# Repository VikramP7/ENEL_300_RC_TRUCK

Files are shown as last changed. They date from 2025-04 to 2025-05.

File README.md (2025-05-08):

*<div align="right"> Vikram Procter, Caleb Garcia, Graham Coleman, Devon Calvin | Feb 12, 2025 </div>*

# DIDSBURY DIDDLERS & Co. Est. 2006 - README

## Project Overview
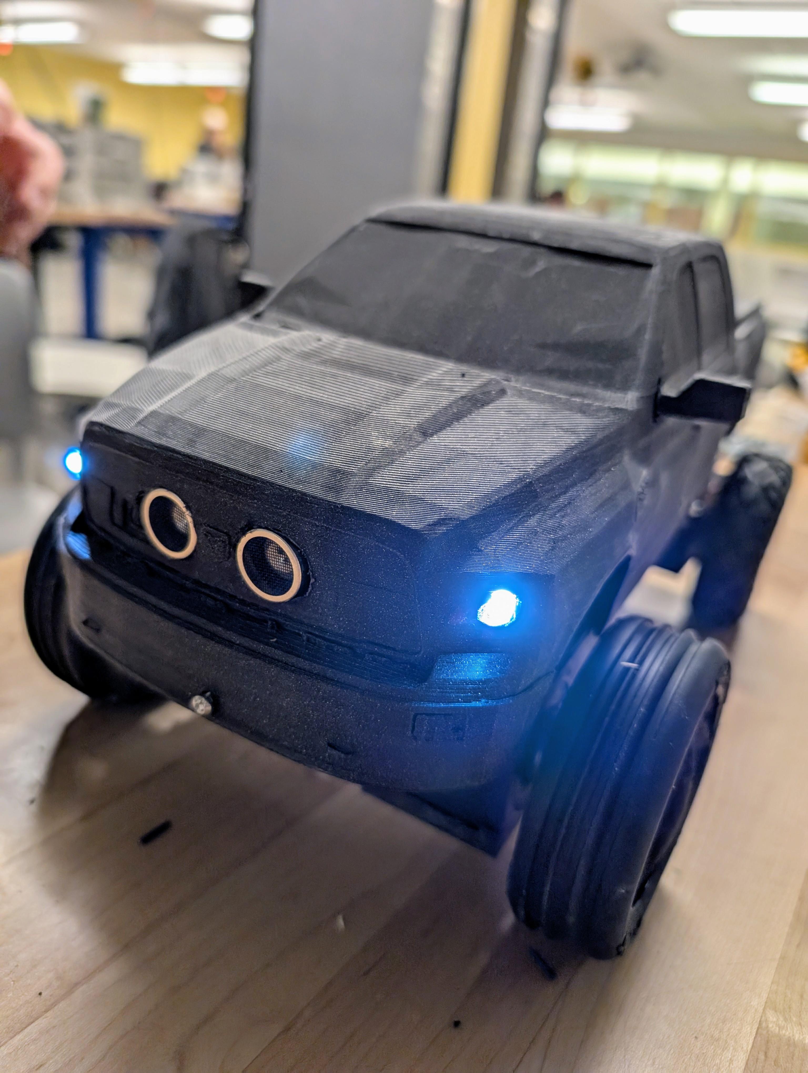
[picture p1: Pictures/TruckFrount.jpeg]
Image of Truck
  
*Photo of finished project*

Remote control car for our ENEL 300 design class at the Schulich School of Engineering at University of Calgary.

Our car integrates a variety of features including distance measurement, metal detection, togglable head/tail lights, tank steering, and more. These features are implemented through 3 custom PCBs, designed in Altium or KiCad. Wireless locomotion control and light control is implemented using the HC-05 Bluetooth transceiver module. The physical design was inspired by a RAM 3500 Cummins 6.7 Twin Turbo and its stereotypical owner *(Devon)*. This allowed us to bring a part of Alberta culture to the academic environment through innovation and design.

## Team Dynamic
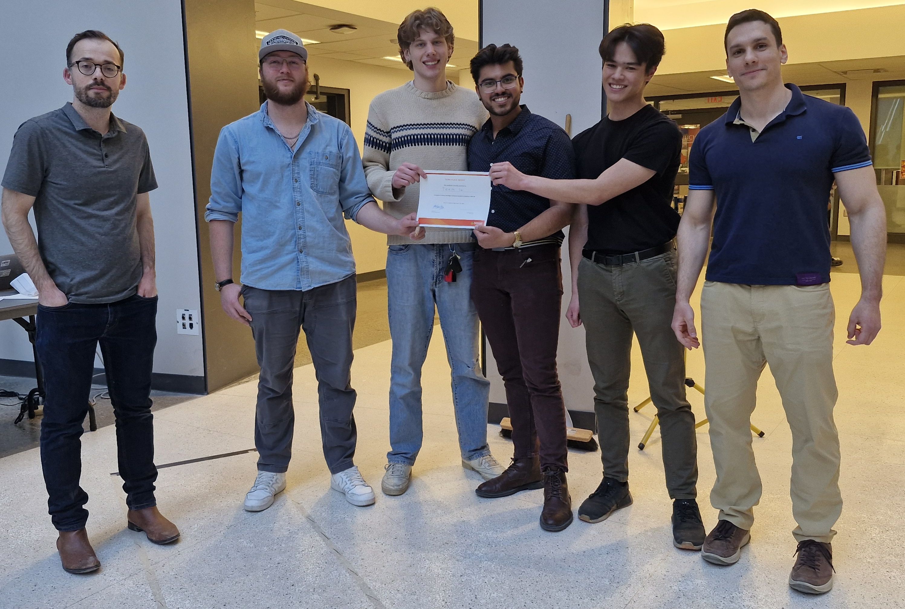
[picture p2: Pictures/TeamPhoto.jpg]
Group Photo w/ truck
  
*Image of Team Members and Professors: Dr. Philippe Gray, Devon Calvin, Graham Coleman, Vikram Procter, Caleb Garcia, and Dr. Flavio Alegretti Ramos; respectively from left to right*

The workload of the various systems was divided amongst us based on interest and skill. Coleman was responsible for implementing metal detection and distance measurement, in addition to working on Bluetooth communications, and controller design. Procter was responsible for ECU, power regulation, inter-board communication, general code management and review. Garcia was responsible for software development, 3D design and printing, and product selection. Calvin was responsible for motor driver development, 3D design, and Bluetooth communications.

## Systems Overview
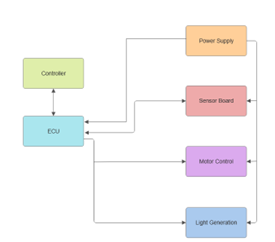
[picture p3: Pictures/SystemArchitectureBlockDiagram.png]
SystemArchitectureBlockDiagram
  
*Block diagram overview of electronic board functionality*

The block diagram shows the operating architecture of the RC truck describing the PCB boards connections to each other. There were four custom PCBs in which 3 were used in the final design. Each board design function and integration are described in detail in the sections bellow. 

All boards excluding the controller interface with each other using an I2C bus, the ECU acts as the master on the bus and the Sensor Board/Motor Control Board act as slaves on the bus. The Controller board interfaces with the ECU alone using USART over a Bluetooth connection.

The four boards include: 
- **Controller Board** | not utilized in the final design, but would have been used within the controller to offer UI to user.
- **ECU** | Electronics Control Board, acts to integrate functionality of all other boards along with power supply regulation.
- **Sensor Board** | Finds and relays metal detection and distance sensing data.
- **Motor Control Board** | Houses motor drivers and receives data for locomotion control of vehicle.

## Sensors Systems (Sensor Board)
### Metal Detector
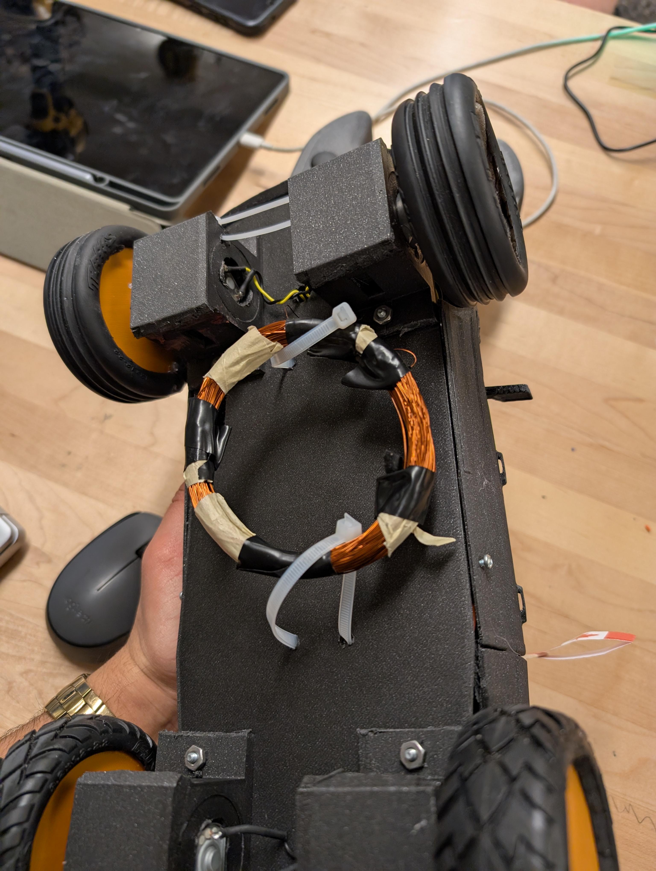
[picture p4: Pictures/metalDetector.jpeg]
Picture of Metal detector coil
  
*Metal detection inductor coild attatched to bottom of vehicle*

The metal detection system is designed around a 555 timer IC and inductor capacitor (LC) circuit. The 555 timer produces an AC input in which the frequency response output varies with changes in inductance. By exposing the inductor coil placed on the bottom of the car to a copper sheet the inductance of the coil changes and the frequency of the output changes in response.

The sensor board uses a built in timer module of the AVR128DB28 to measure the frequency of the LC circuit. By tuning a threshold, the recorded frequency could be used to identify if the coil was exposed to metal. This information was then relayed over I<sup>2</sup>C to the ECU.

### Distance Sensor
An ultrasonic distance sensor was used to find the distance of the nearest object in front of the car. The Sensor Board interfaced with the ultrasonic providing the appropriate 10 microsecond trigger and recording the echo. This raw echo data was transmitted over I<sup>2</sup>C to the ECU.

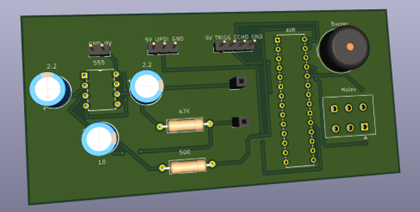
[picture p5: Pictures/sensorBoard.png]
Sensor board Schematic
  
*Render of Sensor Board PCB*

## Power Systems (ECU)
### Battery
The battery we selected has a capacity of 3000 mAh with a nominal voltage of 12.6V, this was used to supply power to all boards and the motors excluding the metal detection circuit. This battery consisted of 4 cells with integrated charging and level balancing technology.

Through estimates of maximum current draw, the runtime on one full charge was calculated to be 228 minutes. This battery was initially chosen as previously we had sourced higher power motors; these higher power motors made the battery selection more reasonable for runtime calculations. However, in switching motors we decided not to change our battery selection as it was still sufficient for operation.

### Voltage Regulation

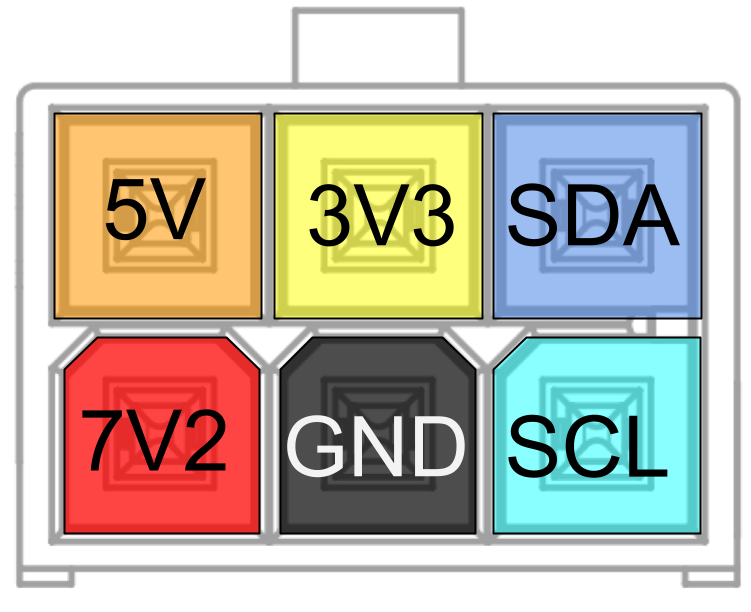
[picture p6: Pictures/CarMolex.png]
Picture of Molex connector standard
  
*Custom Standard for Molex Connector*

To produce the voltage 5V and 3.3V lines linear dropout regulators (LDOs) were used. These regulators were placed on the ECU and using a custom Molex connector, voltage levels were distributed to other boards (motor control board, and sensor board).

### Power Switch
The power switch uses a PMOS high side switch topology to switch between three states: off, USB power, and battery power. For regular operation 12.6V battery is used, however for development and debugging 5V USB can be used. This switch system allows for isolation between the battery and USB for safe operation.

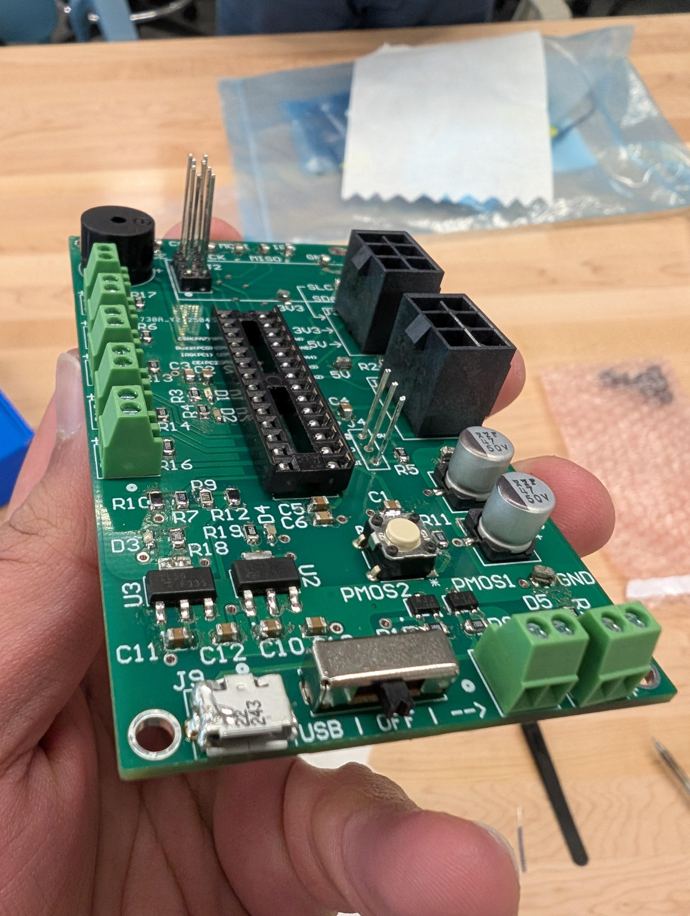
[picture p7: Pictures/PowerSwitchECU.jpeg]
Picture of Bottom of ECU
  *Image of ECU Showing Power Switch*

## Communications Systems (ECU + Others)
### Bluetooth USART

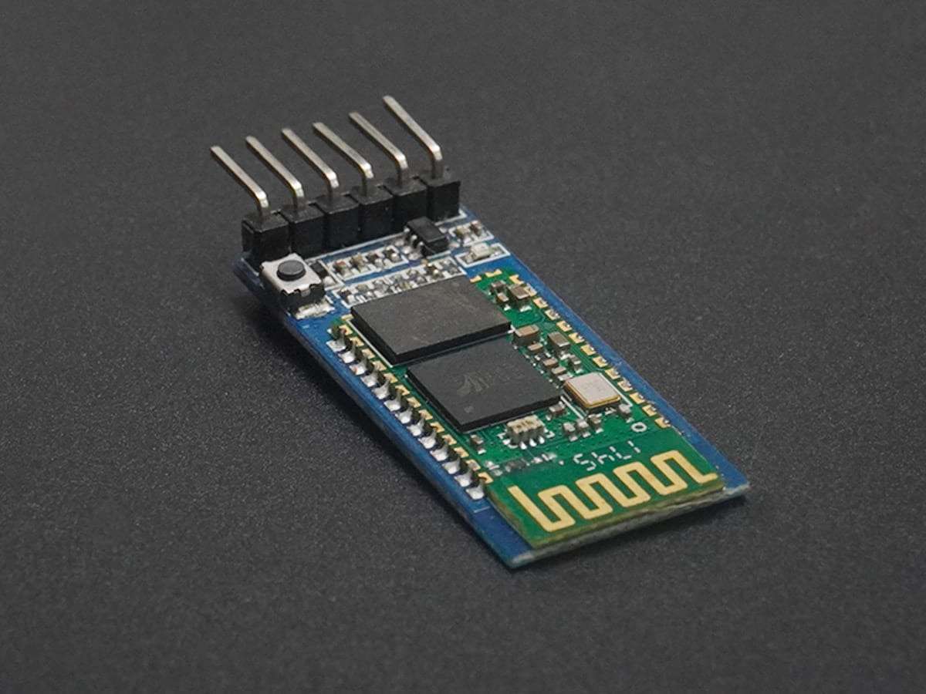
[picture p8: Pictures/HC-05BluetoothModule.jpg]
Picture of HC-05
  
*[Image Cred.](https://www.electronicwings.com/sensors-modules/bluetooth-module-hc-05-) HC-05 Bluetooth Module used in the vehicle*

The ECU board and controller boards preformed wireless communications via a USART over Bluetooth communications module [HC-05](https://www.electronicwings.com/sensors-modules/bluetooth-module-hc-05-). The controller board would send movement control and light switch position data to the ECU board, describing positions of single axis joy sticks and if the lights should be on or not. The ECU board would send sensor data including distance and metal detection.

Three 8-bit data packets were sent from the controller. Two packets described the left and right joystick position encoded using sign magnitude. And the third packet contained the status of the light switch. 

One 8-bit packet was sent from the ECU to describe metal detection (most significant bit), and distance sensor data encoded in the 7 least significant bits. 

### I<sup>2</sup>C Inter-board Communication
An I<sup>2</sup>C bus was utilized between boards within the vehicle (ECU, Motor Board, and Sensor Board). Connection between boards was accomplished using the same custom Molex connector as described in the power regulation section.

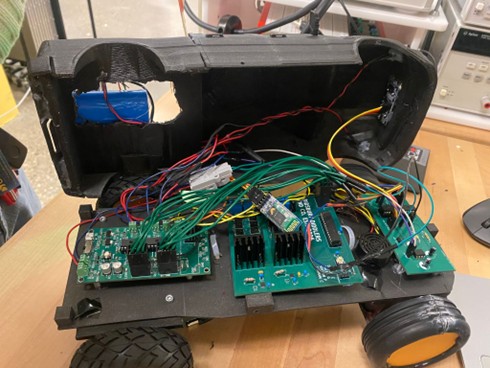
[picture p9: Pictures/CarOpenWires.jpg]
Picture of Car Opened with Wires
  
*3d printed body removed showing wiring*

The ECU hosted the I<sup>2</sup>C bus housing the pull-up resistors and acted as the master on the bus. The ECU would relay motor control data received from the controller board to the Motor Board. The ECU would request data from the Sensor Board, receiving distance and metal detection data. I<sup>2</sup>C communications is a non-blocking function within the super loop of all boards. 

I<sup>2</sup>C packets took a very similar form to USART packets over Bluetooth. The motor board would receive two 8-bit sign-magnitude packets one for each side of the vehicle. Two packets were received from the Sensor Board. The MSB of the first packet described the metal detection data, and the remaining 15 bits described the distance sensor data. The ECU would compress the data to 7 bits before relaying to the controller.

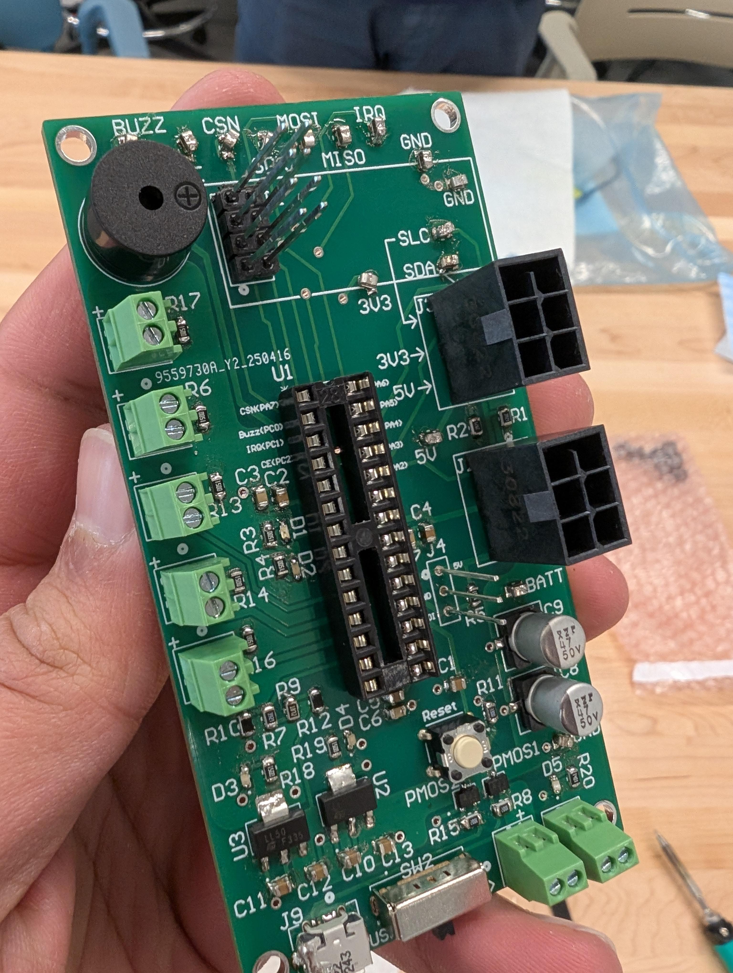
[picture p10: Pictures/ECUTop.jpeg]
Picture of ECU Board
  
*Image of ECU PCB*

## Controller

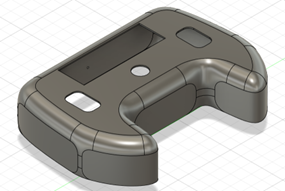
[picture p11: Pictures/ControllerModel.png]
Picture of Controller
  
*3D Model of Controller*

### LCD UI
The 2x16 ASCII LCD selected was equipped with an I<sup>2</sup>C piggy-back-board to allow for fewer required pins for operation. The controller board acted as the master and LCD as slave on the I<sup>2</sup>C bus.

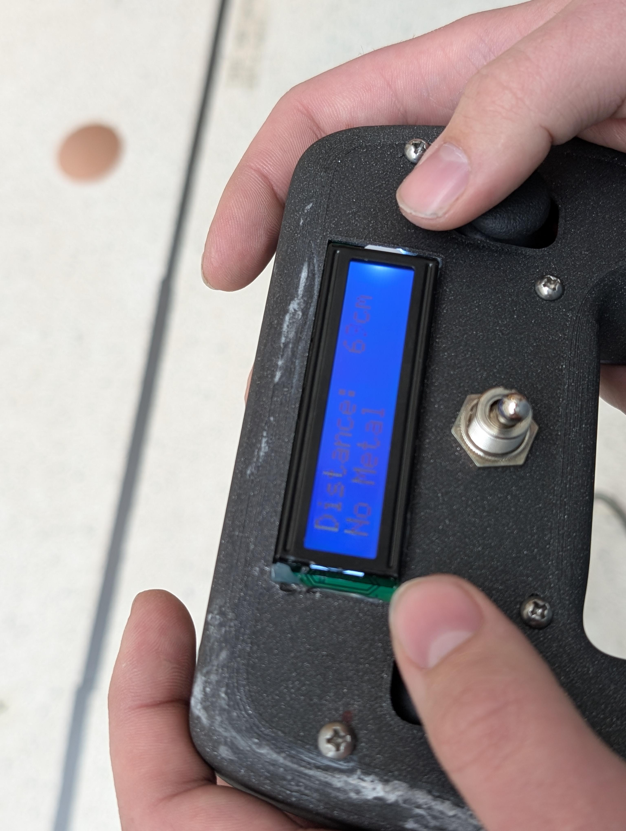
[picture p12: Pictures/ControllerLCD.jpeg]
Picture of LCD on Controller
  
*Controller with LCD display, thumb joysticks and lights switch*

On power up the LCD would display the team name, before displaying the distance data, and metal detection data Custom functions were written to interface with the LCD to allow for ease of formatting the results on the screen, while avoiding having to do floating point calculations. 

### Inputs
The controller was equipped with two single axis joysticks for controlling locomotion and one switch for controlling the lights. The vehicle utilized a tank steering system where each joystick would control the speed of the wheels on one side of the vehicle. The joysticks function as a potentiometer, by creating a voltage divider the change in resistance as the joystick moved was recorded using an ADC on the AVR128DB28. Through the careful design of the voltage divider the AVR128DB28 was able to provide ADC input to a much higher accuracy than needed (12-bit resolution). This value was compressed and encoded to the 8-bit sign-magnitude value transmitted over I<sup>2</sup>C.

Data collected through the input devices and data required for displaying on the LCD was transmitted using USART over Bluetooth using the [HC-05](https://www.electronicwings.com/sensors-modules/bluetooth-module-hc-05-). Although data was compressed for transmission over Bluetooth, it was done in a way that retains accuracy to the level required by the project.   

*A PCB was designed for the controller however due to time and resource constraints the PCB was not assembled and the controller board was constructed using a perfboard*

## Locomotion Systems (Motor Board)
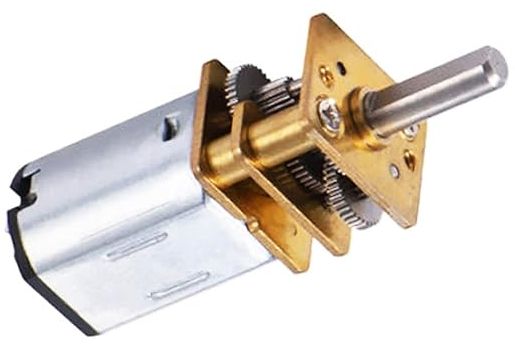
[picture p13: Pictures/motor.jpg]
Picture of Motors
  
*Motors Used in vehicle*

The selected motors are driven using two L298N H-Bridge motor drivers, using 12.6V supplied from the battery with inline Toshiba TCKE812NA E-Fuses for over current protection. As this is a high current board, large polygon pours were used when dealing with high current nets. Thermal reliefs were also removed to improve thermal conduction during operation and max current tolerance. As this board interfaces with large inductive loads, fly back diodes were also used. 

The Motor Control Board is also equipped with an AVR128DB28 to interface with the I<sup>2</sup>C bus and use information received to operate the motor driver ICs. The Motor Control Board receives two 8-bit packets containing the sign-magnitude values for the speeds the motors should be spinning on each side of the vehicle. To control the motor speed a PWM signal generated using the AVR128DB28 was used as an input to the enable pin of the L298N motor drivers. The 8-bit packets are decoded to find the polarity (from sign) and duty of PWM (from magnitude). 

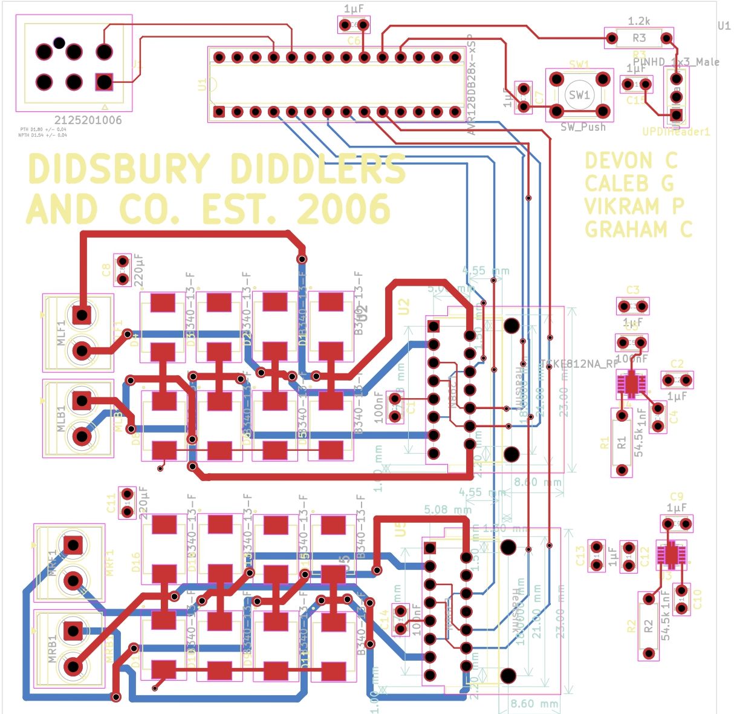
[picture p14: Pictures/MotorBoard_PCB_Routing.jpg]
Picture of Motor Board
  
*PCB routing layout of the Motor Control Board*

## Mechanical Design
The frame and body of the vehicle, along with the controller case was 3d printed. The frame consisted of a baseplate that custom motor bracket mounts were attached to. The frame had holes drilled for connections to motor terminals. The body was printed from a modified 3d model of a RAM 3500 found online. Wheels were also printed and off the shelf rubber tires were fitted to them. All 3d models were scaled to achieve an approximate 1:16 scale to the real truck. All prints were done in PLA, and infill was scaled based on points of high stress.  

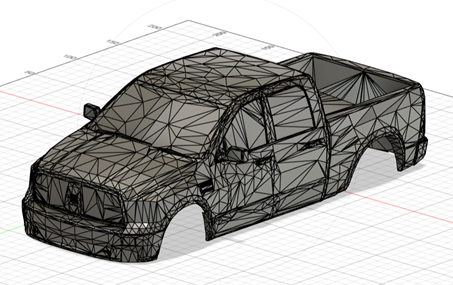
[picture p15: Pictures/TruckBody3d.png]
Picture of 3d Prints
  
*3D Printed Body File*

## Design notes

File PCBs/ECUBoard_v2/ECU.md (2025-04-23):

*<div align="right"> Written by Vikram Procter | Feb 12, 2025 </div>*

# DIDSBURY DIDDLERS & Co. Est. 2006 - ECU Board

## Purpose Overview
- Houses power supply providing voltages for self and other boards
- Provide adequete current and voltage supply for motors
- Connect to other boards using 6 position Molex connector to provide I2C lines and power
- Sends and recieves data over I2C for motor control, distance sensor, metal detection, light control
- If extra ports measure battery voltage
- Control buzzer

## v2 Improvements
- ~~Power indicators for 5V, 3V3, and battery~~
- ~~Fix screw terminals~~
- ~~fix programming header~~ 
- ~~Remove fuse and buck~~
- ~~Lots of test points / vias for osciliscope~~
- ~~Good power switch~~
- ~~Fix Radio connector~~
- ~~Silk screen labels out the oiseau~~
- ~~Mounting holes in the corners~~

## Resource Overview
### Connectors
- Molex Connectors (Board side) [2125201006](https://www.digikey.ca/en/products/detail/molex/2125201006/13693762?s=N4IgTCBcDa4IxgKxgAxxSgbCAugXyA)
- Molex Connector (Wire side) [2125141006](https://www.digikey.ca/en/products/detail/molex/2125141006/13693743?s=N4IgTCBcDa4IxgKxwCxwAzoGwgLoF8g)
- Molex Crimps (in wire side) [2125153102](https://www.digikey.ca/en/products/detail/molex/2125153102/13693772)

### Buzzer
- PWM buzzer should be connected to PA0 or PC0 for comparitor TCA0 waveform generation, use 0 Ohm for config
- Port A or C can be configured in PORTMUX, and specific n pin is enabled in TCAn.CTRLB.CMPnEN
- Tenative Buzzer 5V buzzer [WT-1205](https://www.digikey.ca/en/products/detail/soberton-inc/WT-1205/479674)

### Debug LEDs
- Debug leds will be attached to PORTD, LED are wired active low
- There is a red LED ([SML-D12U1WT86](https://www.digikey.ca/en/products/detail/rohm-semiconductor/SML-D12U1WT86/5843853)) and a green LED ([SML-D12P8WT86](https://www.digikey.ca/en/products/detail/rohm-semiconductor/SML-D12P8WT86/1641798))

### Head Lights, Tail Lights and Light Bar:
- All lights will be connected via screw terminals
- Lights will be controlled through 

### I2C Interface
- Ports PA2 (SDA MS) and PA3 (SCL MS) are used for the two I2C lines
- ECU will be configured as master, other boards are configured as slaves
- The lines connected to the bus are described in the connector section

### Radio SPI Interface
- Using the [NRF24L01+PA+LNA](https://www.amazon.ca/Aideepen-NRF24L01-Transceiver-Breakout-Compatible/dp/B07ZGQ2X7Q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)
- PinOut from header to radio board: 
    - pin(Headerpin)=NAME(radiopin)
    - pin1=MISO(pin7)
    - pin2=SCK(pin5)
    - pin3=CE(pin3)
    - pin4=GND(pin1)
    - pin5=VCC(pin2)
    - pin6=CSN(pin4)
    - pin7=MOSI(pin6)
    - pin8=IRQ(pin8)
- Pin connections to AVR (as described in SPI and pinout sections):
    - AVRpin=NAME=radio header pin
    - PA5=MISO=pin1
    - PA6=SCK=pin2
    - PA4=MOSI=pin7
    - PA7=SS/CSN=pin6
    - PC1=IRQ=pin8
    - PC2=CE=pin3

### Power and Bus Connector
- Refer to following image for connector specifications
Molex Connector Standar
- In the schematic 
    - pin1=SCL
    - pin2=GND
    - pin3=7V2
    - pin4=SDA
    - pin5=3V3
    - pin6=5V

### Microcontroller
- [AVR128DB28](https://www.digikey.ca/en/products/detail/microchip-technology/AVR128DB28-I-SP/12807495) is the main microcontroller
- Placed in dips IC connector [ED281DT](https://www.digikey.ca/en/products/detail/on-shore-technology-inc/ED281DT/4147600)

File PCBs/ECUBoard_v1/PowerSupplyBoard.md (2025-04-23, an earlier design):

*<div align="right"> Written by Vikram Procter | January 11, 2025 </div>*

# DIDSBURY DIDDLERS & Co. Est. 2006 - Power Supply Board

## Purpose Overview
- Provide stable voltage sources for the various boards
- Provide adequete current and voltage supply for motors
- Required voltages is 3V3, 5V, 7.2V (5A)

## Resource Overview
### Power Chips
- 3V3 LDO <a href="https://www.digikey.ca/en/products/detail/stmicroelectronics/LDL1117S33R/7102071">LDL1117S33R</a>
- 5V LDO <a href="https://www.digikey.ca/en/products/detail/stmicroelectronics/LDL1117S50R/7102072">LDL1117S50R</a>
- 7V2 Buck <a href="https://www.digikey.ca/en/products/detail/texas-instruments/LM25085MYX-NOPB/2020207">LM25085MYX</a>

### Interfacing
- <a href="https://www.digikey.ca/en/products/detail/phoenix-contact/1984617/950849">Terminal blocks</a> for 3 voltage outputs and ground
- Terminal blocks for battery input

## Resource Specs
### Current limmiting
-   The Electronic Fuse Regulator [TPS259251DRCR](https://www.digikey.ca/en/products/detail/texas-instruments/TPS259251DRCR/5481850) is used to limit current draw to bellow 5A battery max
-   The limiting resistor $R_{Ilim}=\frac{I_{lim}-0.7}{3*10^{-5}}=142k\Omega$ based on pg.19
-   The $C_{dVdt}=\frac{T_{dVdt}}{10^6*V_{IN}}-70pF$ as described on pg. 15
-   No external capacitor $C_{dVdt}$ is required as thermal shutoff time for application is within acceptable limit as descibed on pg.21
-   The reset of the components are copied from the typical application section (pg.18)

### 3V3 LDO LDL1117S33R
-   Fixed Value, only extra components are caps specified by data sheet
### 5V LDO LDL1117S50R
-   Fixed Value, only extra components are caps specified by data sheet
### 7V2 Buck LM25085MYX
-   Output Voltage: EQ(15) Pg(18)
    - $R_{FB2}/R_{FB1}=(V_{out}/1.25)-1$
    - We are looking for $V_{out}=7.2V$ therefore $R_{FB2}/R_{FB1}=4.76$
    - These resistor values are supposed to be between 1k and 20k, so $R_{FB2}=18.7k\Omega, R_{FB1}=3.9k\Omega$
-   Finding the $R_T$ resistor:
    - Using the [STS5P3LLH6](https://www.digikey.ca/en/products/detail/stmicroelectronics/STS5P3LLH6/5244768) pFET with delay time difference (pg.3, pFET resistor):
    - $t_D=t_{d(off)}-t_{d(on)}=19.2ns-5.4ns=13.8ns$ 
    - Using equation 5 (pg. 13)
    - $R_T=\frac{Vout\times(Vin-1.56V)}{1.45\times10^{-7}\times Vin \times Fs}-\frac{t_D\times(Vin-1.56)}{1.47\times 10^{-7}}-1.4$
    - With $F_s=300kHz$ then $R_T=141.6k\Omega$
    - Yeilds duty of 0.6, and a $T_{ON}=2027.6ns$
-   Finding L1:
    - Current ripple amplitude, should be 20% of max current load
    - $I_{OR}=4A\times 20\% = 0.8A$
    - Based on a max input voltage of 12.6V, $L1=13.7\mu H$
-   Setting Current limmiting:
    - From pg. 14, eq.9: $I_{CL}=40\mu A \times \frac{R_{ADJ}}{R_{SEN}}$
    - This yeilds $\frac{R_{ADJ}}{R_{SEN}}=100000$ we can use $R_{ADJ}=1.392k\Omega$ and $R_{SEN}=10m\Omega$
-   Finding Cout:
    - $C_{out}$ can be any value between $2-40\mu F$
-   Finding R3, C1, C2:
    - Found $V_A=6.98$, and $R3\times C1=1.632\times 10^{-4}$
    - $C1 = 4000pF$, and $R3 = 40.8k\Omega$
    - C2 just has to be large therefore $C2=0.1\mu F$
-   The Cvcc cap val is recommended to be 0.47uF (pg.22) and should be placed close to Vin and Vcc pins

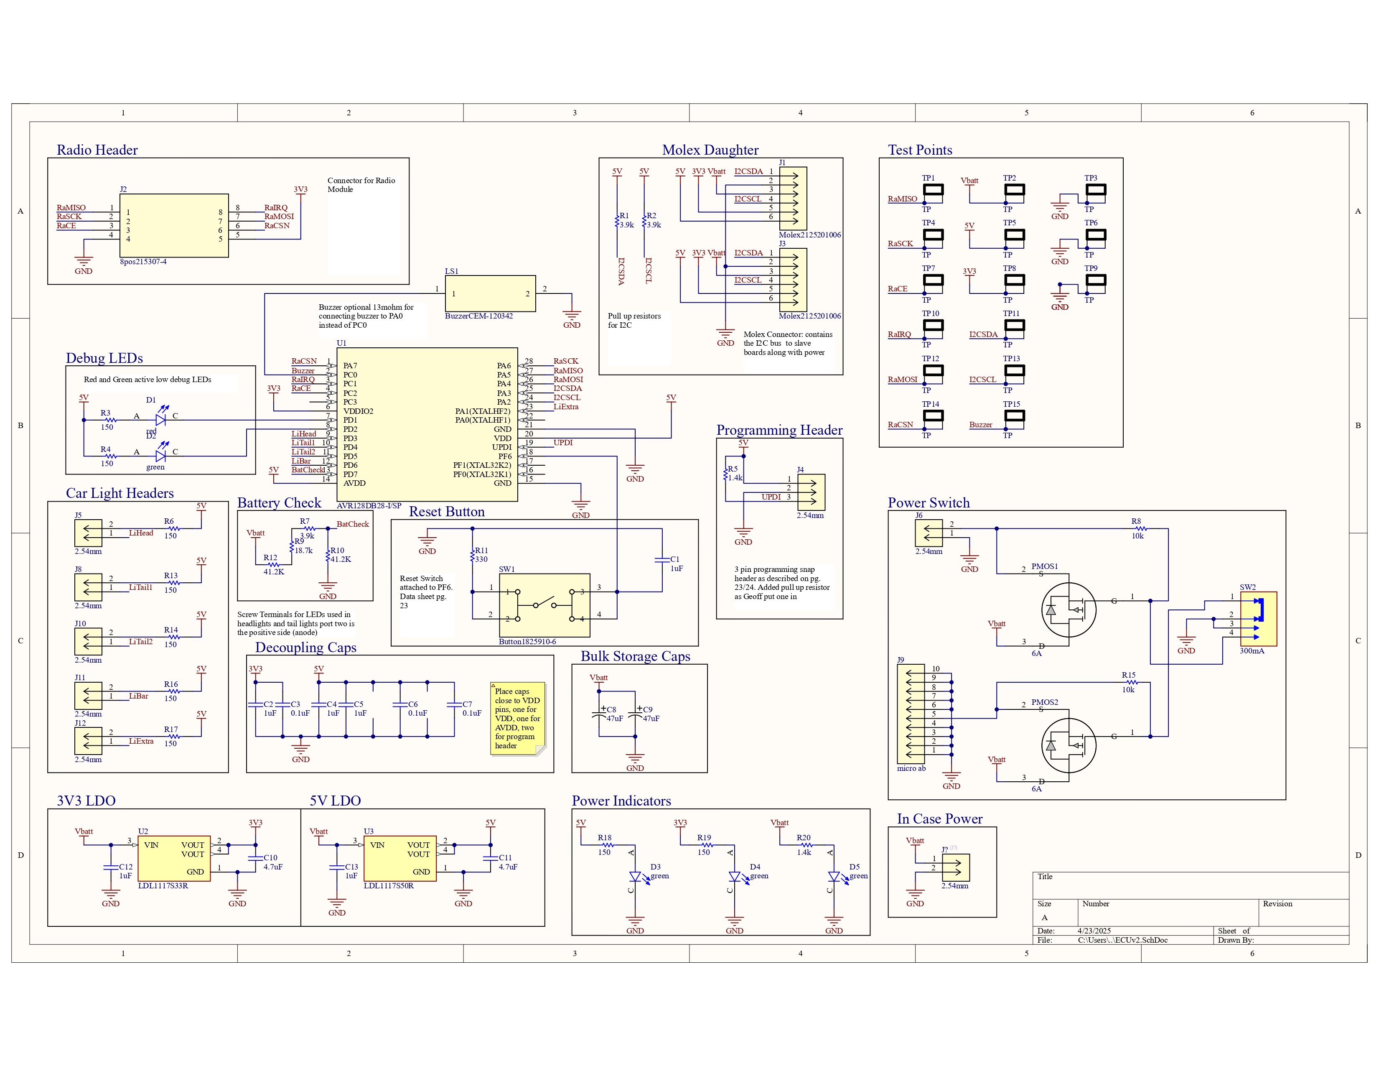
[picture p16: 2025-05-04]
Pictures/ECUv2_Schematic.jpg

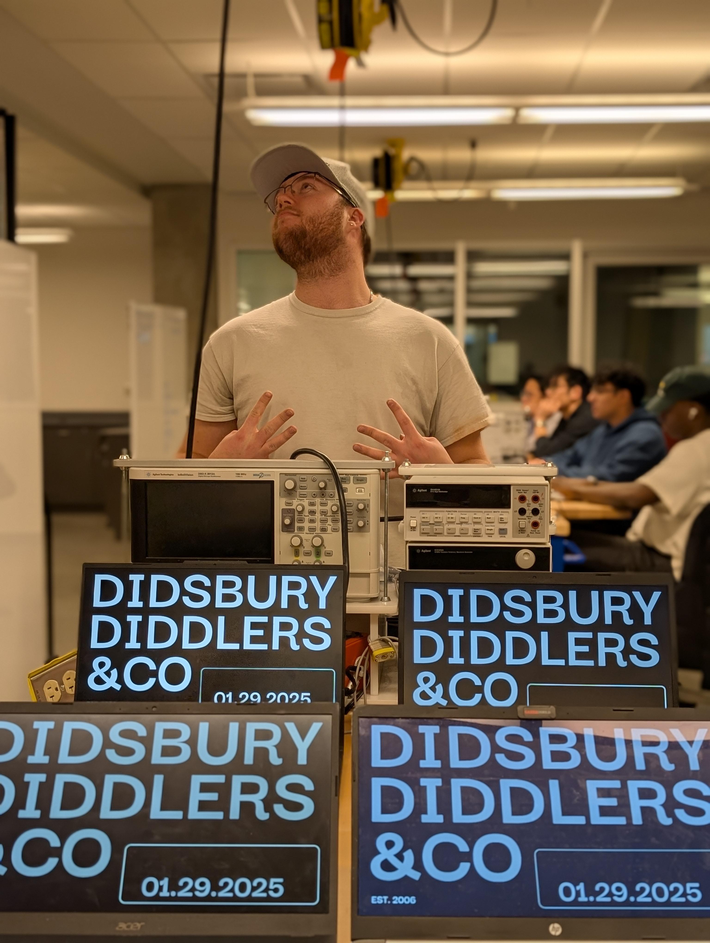
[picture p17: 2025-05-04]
Pictures/Devon.jpeg

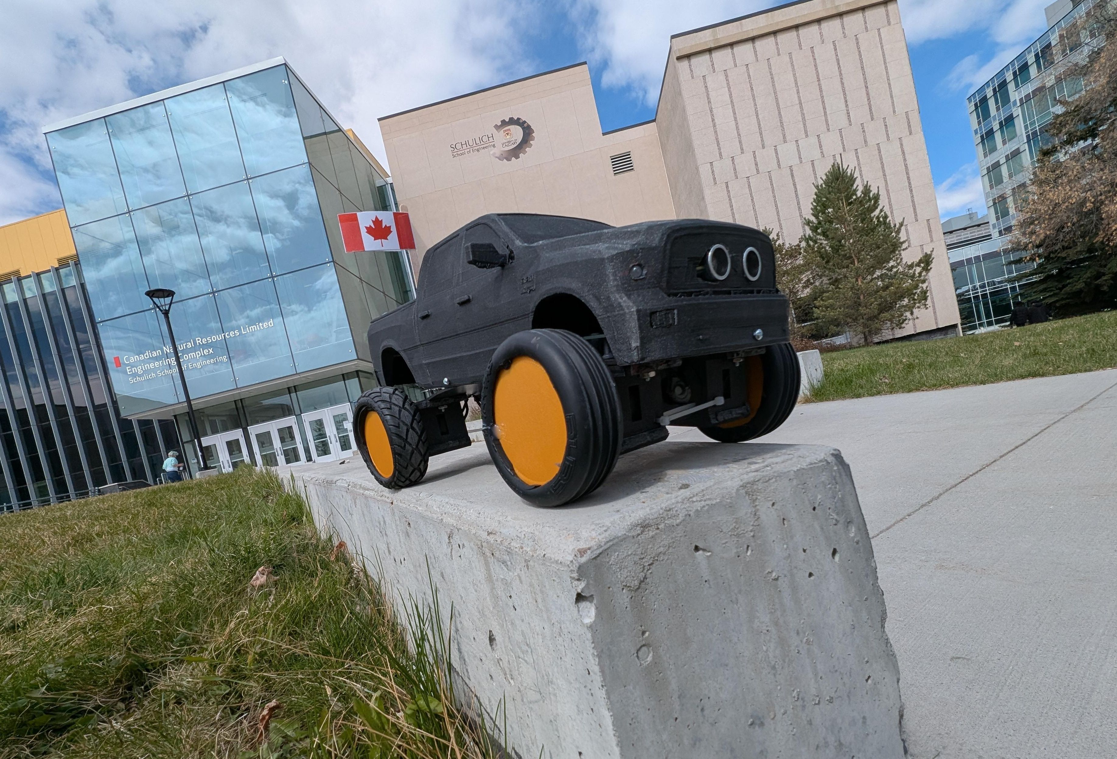
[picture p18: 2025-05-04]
Pictures/Gblock.jpg

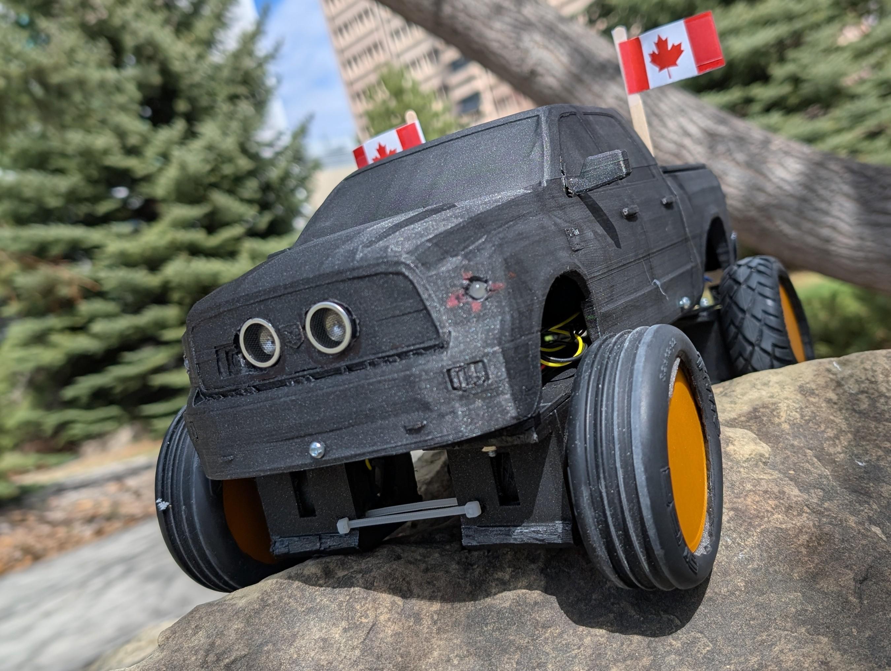
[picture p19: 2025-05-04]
Pictures/OutDoors.jpeg

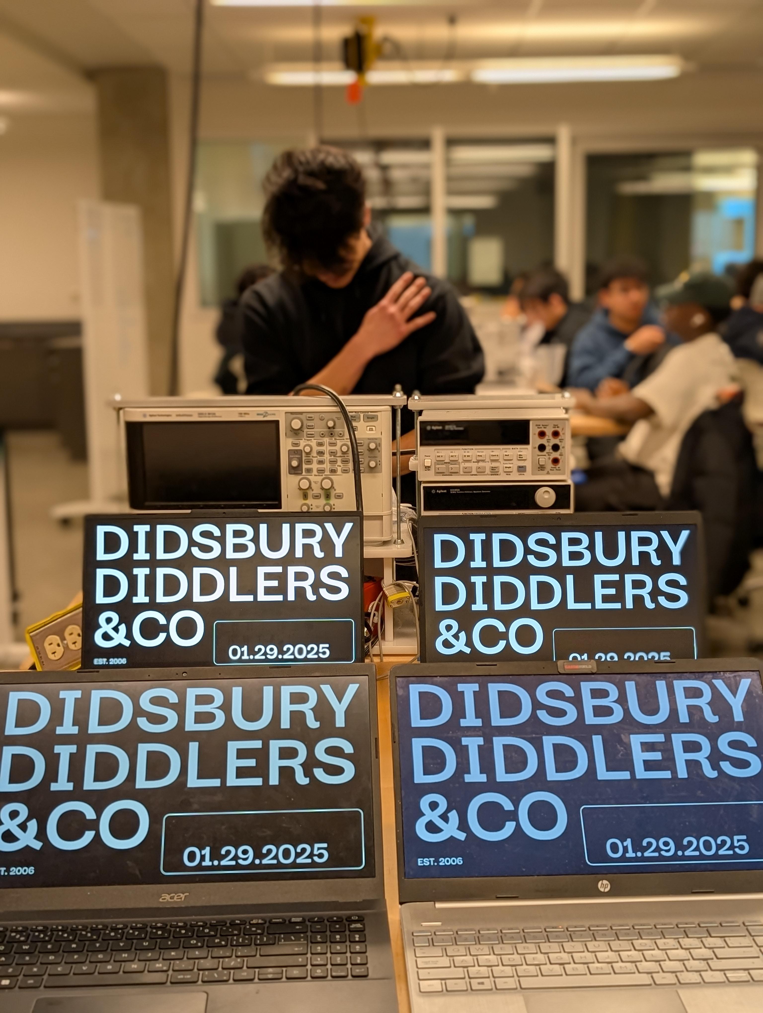
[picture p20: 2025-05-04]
Pictures/Graham.jpeg

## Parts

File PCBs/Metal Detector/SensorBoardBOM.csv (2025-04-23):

Reference | Value | Datasheet | Footprint | Qty | DNP
BZ1 | Buzzer | ~ | Buzzer_Beeper:Buzzer_TDK_PS1240P02BT_D12.2mm_H6.5mm | 1
C1,C2 | 2.2uF | ~ | Capacitor_THT:CP_Radial_D8.0mm_P2.50mm | 2
C3 | 10uF | ~ | Capacitor_THT:CP_Radial_D8.0mm_P2.50mm | 1
J1 | Conn_01x02_Pin | ~ | Connector_PinHeader_2.54mm:PinHeader_2x01_P2.54mm_Vertical | 1
J2 | 1724470206 |  | 1724470206:MOLEX_1724470206 | 1
J3,J4,J5,J6,J7,J8 | Conn_01x01_Pin | ~ | -- mixed values -- | 6
J9 | Conn_01x03_Pin | ~ |  | 1
R1 | 47K | ~ | Resistor_THT:R_Axial_DIN0309_L9.0mm_D3.2mm_P12.70mm_Horizontal | 1
R2 | 500 | ~ | Resistor_THT:R_Axial_DIN0309_L9.0mm_D3.2mm_P12.70mm_Horizontal | 1
U1 | NE555D | http://www.ti.com/lit/ds/symlink/ne555.pdf | 555:P8 | 1
U2 | AVR128DB28x-xSP | https://ww1.microchip.com/downloads/en/DeviceDoc/AVR128DB28-32-48-64-DataSheet-DS40002247A.pdf | AVR28DB28-I/SP:SPDIP28_SP_MCH | 1

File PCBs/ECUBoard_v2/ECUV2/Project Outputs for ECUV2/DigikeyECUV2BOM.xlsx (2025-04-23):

Country of Origin may be different at time of shipment.
The HTSUS and ECCN information shown is for informational purposes only and is not a representation or warranty as to the accuracy or reliability of these classifications. All information is provided "as is" and is subject to change without notice. Any use made of the information provided is without recourse to Digi-Key and at the user's risk.
Index | Manufacturer Part Number | Manufacturer Name | Description | Availability | Stock Status | Assemblies | Attrition % | Requested Quantity 1 | Pack Quantity 1 | Pack Type 1 | Digi-Key Part Number 1 | Unit Price 1 | Extended Price 1 | Minimum Order Quantity 1 | Requested Quantity 2 | Pack Quantity 2 | Pack Type 2 | Digi-Key Part Number 2 | Unit Price 2 | Extended Price 2 | Minimum Order Quantity 2 | Customer Reference | Requested Part Number | Lead Weeks | Datasheet | Reference Designator | US Import Tariff | Note | Part Status | RoHS Status | Moisture Sensitivity Level (MSL) | ECCN | HTSUS | Country of Origin | Environmental Information | Original Part numbers | REACH Status | Unit of Measure | Image | Product Notes
1 | SLW-1277545-2A-RA-S-D | Same Sky (Formerly CUI Devices) | 12.7 X 7.5 X 4.5 MM, 2 MM RAISED | 2,799 | In Stock | 2 |  | 1 | 2 | Box | 2223-SLW-1277545-2A-RA-S-D-ND | 0.59000 | $1.18 | 1 |  |  |  |  |  |  |  | SW2 | 2223-SLW-1277545-2A-RA-S-D-ND | 7 | https://www.cuidevices.com/product/resource/slw-1277545-2a-ra-s-d.pdf |  | N/A |  | Active | ROHS3 Compliant | Not Applicable | EAR99 | 8536.50.9050 | China | https://mm.digikey.com/Volume0/opasdata/d220001/medias/common/6477/slw-1277545-2a-ra-s-d.html | 2223-SLW-1277545-2A-RA-S-D-ND |  | EACH | https://mm.digikey.com/Volume0/opasdata/d220001/medias/images/6285/MFG_SLW-1277545-2A-RA-S-D.jpg
2 | OSTVN02A150 | On Shore Technology Inc. | TERM BLK 2P SIDE ENT 2.54MM PCB | 12,090 | In Stock | 2 |  | 7 | 14 | Bulk | ED10561-ND | 0.96700 | $13.54 | 1 | 4 | 10 | Bulk | ED10561-ND | 0.96700 | $9.67 | 1 | J6-J12 | ED10561-ND | 8 | https://mm.digikey.com/Volume0/opasdata/d220001/medias/docus/1123/OSTVNXXA150.pdf |  | N/A |  | Active | ROHS3 Compliant | 1 (Unlimited) | EAR99 | 8536.90.4000 | China | https://www.on-shore.com/wp-content/uploads/RoHS3_REACH-STATEMENT-240.pdf | ED10561-ND | REACH Unaffected | EACH | https://mm.digikey.com/Volume0/opasdata/d220001/medias/images/410/OSTVN02A150.JPG
3 | 215307-4 | TE Connectivity AMP Connectors | CONN RCPT 8POS 0.1 GOLD PCB | 4,050 | In Stock | 2 |  | 1 | 2 | Tray | A106657-ND | 1.89000 | $3.78 | 1 |  |  |  |  |  |  |  | J2 | 98K6517 | 31 | https://www.te.com/usa-en/product-215307-4.datasheet.pdf |  | N/A |  | Active | ROHS3 Compliant | 1 (Unlimited) | EAR99 | 8536.69.4040 | Poland | http://www.te.com/commerce/alt/SinglePartSearch.do?PN=215307-4&dest=stmt | 98K6517 | Vendor Undefined | EACH | https://mm.digikey.com/Volume0/opasdata/d220001/medias/images/411/215307-4.JPG
4 | CL21A475KAQNNNE | Samsung Electro-Mechanics | CAP CER 4.7UF 25V X5R 0805 | 2,451,723 | In Stock | 2 |  | 2 | 4 | Cut Tape (CT) | 1276-1244-1-ND | 0.15000 | $0.60 | 1 | 6 | 12 | Cut Tape (CT) | 1276-1244-1-ND | 0.08600 | $1.03 | 1 | C10,C11 | 1276-1244-1-ND | 22 | https://mm.digikey.com/Volume0/opasdata/d220001/medias/docus/41/CL21A475KAQNNNE_Spec.pdf |  | N/A |  | Active | ROHS3 Compliant | 1 (Unlimited) | EAR99 | 8532.24.0020 | China | https://www.samsungsem.com/files/fileDown.do?key=ed1dfdfa-645e-4252-b707-17f9b1502dd1|https://www.samsungsem.com/global/support/certificate/product-stewardship.do | 1276-1244-1-ND | REACH Unaffected | EACH | https://mm.digikey.com/Volume0/opasdata/d220001/medias/images/2537/Ceramic-Capacitor-CL-Series.jpg
5 | CC0805KRX7R9BB104 | YAGEO | CAP CER 0.1UF 50V X7R 0805 | 2,956,037 | In Stock | 2 |  | 3 | 6 | Cut Tape (CT) | 311-1140-1-ND | 0.12000 | $0.72 | 1 | 6 | 12 | Cut Tape (CT) | 311-1140-1-ND | 0.05100 | $0.61 | 1 | C3,C6,C7 | 311-1140-1-ND | 16 | https://www.yageo.com/upload/media/product/productsearch/datasheet/mlcc/UPY-GPHC_X7R_6.3V-to-250V_24.pdf |  | N/A |  | Active | ROHS3 Compliant | 1 (Unlimited) | EAR99 | 8532.24.0020 | Taiwan |  | 311-1140-1-ND | REACH Unaffected | EACH | https://mm.digikey.com/Volume0/opasdata/d220001/medias/images/4322/cut-tape-render.jpg
6 | CL21B105KBFNNNE | Samsung Electro-Mechanics | CAP CER 1UF 50V X7R 0805 | 129,666 | In Stock | 2 |  | 6 | 12 | Cut Tape (CT) | 1276-1029-1-ND | 0.04500 | $0.54 | 1 | 8 | 16 | Cut Tape (CT) | 1276-1029-1-ND | 0.04500 | $0.72 | 1 | C1,2,4,5,12,13 | 1276-1029-1-ND | 22 | https://mm.digikey.com/Volume0/opasdata/d220001/medias/docus/609/CL21B105KBFNNNE_Spec.pdf |  | N/A |  | Active | ROHS3 Compliant | 1 (Unlimited) | EAR99 | 8532.24.0020 | Philippines | https://www.samsungsem.com/files/fileDown.do?key=ed1dfdfa-645e-4252-b707-17f9b1502dd1|https://www.samsungsem.com/global/support/certificate/product-stewardship.do | 1276-1029-1-ND | REACH Unaffected | EACH | https://mm.digikey.com/Volume0/opasdata/d220001/medias/images/2537/Ceramic-Capacitor-CL-Series.jpg
7 | 2125201006 | Molex | MINI-FIT MAX 6CKT HDR VERT | 182 | In Stock | 2 |  | 1 | 2 | Tray | 900-2125201006-ND | 3.28000 | $6.56 | 1 |  |  |  |  |  |  |  | J1,J3 | 212520-1006 | 16 | https://www.molex.com/webdocs/datasheets/pdf/en-us/2125201006_PCB_HEADERS.pdf |  | N/A |  | Active | ROHS3 Compliant | 1 (Unlimited) | EAR99 | 8536.69.4040 | Mexico |  | 212520-1006 | REACH Unaffected | EACH | https://mm.digikey.com/Volume0/opasdata/d220001/medias/images/3766/MFG_2125201010.jpg
8 | RC0805FR-07150RL | YAGEO | RES 150 OHM 1% 1/8W 0805 | 976,090 | In Stock | 2 |  | 9 | 18 | Cut Tape (CT) | 311-150CRCT-ND | 0.02300 | $0.41 | 1 | 12 | 24 | Cut Tape (CT) | 311-150CRCT-ND | 0.02300 | $0.55 | 1 |  | 311-150CRCT-ND | 18 | https://www.yageo.com/upload/media/product/products/datasheet/rchip/PYu-RC_Group_51_RoHS_L_12.pdf |  | N/A |  | Active | ROHS3 Compliant | 1 (Unlimited) | EAR99 | 8533.21.0030 | Taiwan | https://www.yageo.com/en/Download/Index/certificates#rchip | 311-150CRCT-ND | REACH Unaffected | EACH | https://mm.digikey.com/Volume0/opasdata/d220001/medias/images/4322/cut-tape-render.jpg
9 | RMCF0805FT3K92 | Stackpole Electronics Inc | RES 3.92K OHM 1% 1/8W 0805 | 46,451 | In Stock | 2 |  | 3 | 10 | Cut Tape (CT) | RMCF0805FT3K92CT-ND | 0.04000 | $0.40 | 1 | 6 | 12 | Cut Tape (CT) | RMCF0805FT3K92CT-ND | 0.04000 | $0.48 | 1 | R1,R2,R7 | RMCF0805FT3K92CT-ND | 17 | https://www.seielect.com/catalog/sei-rmcf_rmcp.pdf |  | N/A |  | Active | ROHS3 Compliant | 1 (Unlimited) | EAR99 | 8533.21.0030 | Taiwan | https://www.seielect.com/catalog/SEI-RoHS_Compliance_Status.pdf|https://www.seielect.com/catalog/reach.pdf|https://www.seielect.com/catalog/sei-coc%20prop%2065.pdf | RMCF0805FT3K92CT-ND | REACH Unaffected | EACH | https://mm.digikey.com/Volume0/opasdata/d220001/medias/images/639/0805-RMCF-Series.jpg
10 | RMCF0805FT10K0 | Stackpole Electronics Inc | RES 10K OHM 1% 1/8W 0805 | 1,368,731 | In Stock | 2 |  | 2 | 10 | Cut Tape (CT) | RMCF0805FT10K0CT-ND | 0.04000 | $0.40 | 1 |  |  |  |  |  |  |  | R8,R15 | RMCF0805FT10K0CT-ND | 17 | https://www.seielect.com/catalog/sei-rmcf_rmcp.pdf |  | N/A |  | Active | ROHS3 Compliant | 1 (Unlimited) | EAR99 | 8533.21.0030 | Taiwan | https://www.seielect.com/catalog/SEI-RoHS_Compliance_Status.pdf|https://www.seielect.com/catalog/reach.pdf|https://www.seielect.com/catalog/sei-coc%20prop%2065.pdf | RMCF0805FT10K0CT-ND | REACH Unaffected | EACH | https://mm.digikey.com/Volume0/opasdata/d220001/medias/images/4322/cut-tape-render.jpg
11 | RMCF0805FT18K7 | Stackpole Electronics Inc | RES 18.7K OHM 1% 1/8W 0805 | 213,767 | In Stock | 2 |  | 1 | 2 | Cut Tape (CT) | RMCF0805FT18K7CT-ND | 0.16000 | $0.32 | 1 | 5 | 10 | Cut Tape (CT) | RMCF0805FT18K7CT-ND | 0.04000 | $0.40 | 1 | R9 | RMCF0805FT18K7CT-ND | 17 | https://www.seielect.com/catalog/sei-rmcf_rmcp.pdf |  | N/A |  | Active | ROHS3 Compliant | 1 (Unlimited) | EAR99 | 8533.21.0030 | Taiwan | https://www.seielect.com/catalog/SEI-RoHS_Compliance_Status.pdf|https://www.seielect.com/catalog/reach.pdf|https://www.seielect.com/catalog/sei-coc%20prop%2065.pdf | RMCF0805FT18K7CT-ND | REACH Unaffected | EACH | https://mm.digikey.com/Volume0/opasdata/d220001/medias/images/2597/MFG_RMC%20SERIES.jpg
12 | CRCW080541K2FKEA | Vishay Dale | RES SMD 41.2K OHM 1% 1/8W 0805 | 28,658 | In Stock | 2 |  | 2 | 10 | Cut Tape (CT) | 541-41.2KCCT-ND | 0.06800 | $0.68 | 1 |  |  |  |  |  |  |  | R10,R12 | CRCW080541K2FKEA | 14 | https://www.vishay.com/docs/20035/dcrcwe3.pdf |  | N/A |  | Active | ROHS3 Compliant | 1 (Unlimited) | EAR99 | 8533.21.0030 | Israel |  | CRCW080541K2FKEA | REACH Unaffected | EACH | https://mm.digikey.com/Volume0/opasdata/d220001/medias/images/4849/541_CRCW-0805-%282125metric%29.jpg
13 | SSM3J372R,LF | Toshiba Semiconductor and Storage | MOSFET P-CH 30V 6A SOT23F | 64,640 | In Stock | 2 |  | 3 | 10 | Cut Tape (CT) | SSM3J372RLFCT-ND | 0.32800 | $3.28 | 1 |  |  |  |  |  |  |  | PMOS1,PMOS2 | SSM3J372RLFCT-ND | 16 | https://toshiba.semicon-storage.com/info/docget.jsp?did=59199&prodName=SSM3J372R |  | N/A |  | Active | ROHS3 Compliant | 1 (Unlimited) | EAR99 | 8541.29.0095 | Thailand |  | SSM3J372RLFCT-ND | REACH Unaffected | EACH | https://mm.digikey.com/Volume0/opasdata/d220001/medias/images/2588/SOT-23-3%20Flat%20Leads%20PKG.jpg
14 | SML-D12P8WT86 | Rohm Semiconductor | LED GREEN DIFFUSED 1608 SMD | 0 | Normally Stocking | 2 |  | 6 | 12 | Cut Tape (CT) | 846-SML-D12P8WT86CT-ND | 0.15100 | $1.81 | 1 |  |  |  |  |  |  |  | D2,D3,D4,D5 | 846-SML-D12P8WT86CT-ND | 10 | https://www.rohm.com/datasheet?p=SML-D12P8W&dist=Digi-key&media=referral&campaign=Digi-key |  | N/A |  | Active | ROHS3 Compliant | 3 (168 Hours) | EAR99 | 8541.41.0000 | Malaysia | https://fscdn.rohm.com/en/techdata_basic/led/constitution_materials/const_led_SML-D1x-e.pdf|https://fscdn.rohm.com/en/techdata_basic/led/esd/esd-sml-d12x8w_series.pdf | 846-SML-D12P8WT86CT-ND | REACH Unaffected | EACH | https://mm.digikey.com/Volume0/opasdata/d220001/medias/images/6336/846%7E1608%280603-0.55%29%7E%7E2.jpg
15 | RCTCTE | KOA Speer Electronics, Inc. | PC TEST POINT CHIP | 7,431 | In Stock | 2 |  | 15 | 30 | Cut Tape (CT) | 2019-RCTCTECT-ND | 0.15480 | $4.64 | 1 | 17 | 34 | Cut Tape (CT) | 2019-RCTCTECT-ND | 0.15480 | $5.26 | 1 | TP1 | 2019-RCTCTECT-ND | 9 | https://www.koaspeer.com/pdfs/RC.pdf |  | N/A |  | Active | ROHS3 Compliant | 1 (Unlimited) | EAR99 | 8536.90.4000 | Japan | https://www.koaglobal.com/-/media/Files/KOA_Global/product/common/rohs/Certificate_of_RoHS_Compliance_July2024.pdf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|https://mm.digikey.com/Volume0/opasdata/d220001/medias/docus/5718/2019_KOA%20Speer%20RoHS3%20Statement.pdf | 2019-RCTCTECT-ND | REACH Unaffected | EACH | https://mm.digikey.com/Volume0/opasdata/d220001/medias/images/3698/KOA-RCT-0805.JPG | Non Cancellable Non Returnable.
16 | 0475900001 | Molex | CONN RCPT MICRO USB AB 5P SMD RA | 37,888 | In Stock | 2 |  | 1 | 2 | Cut Tape (CT) | WM17144CT-ND | 1.13000 | $2.26 | 1 |  |  |  |  |  |  |  | J9 | WM17144CT-ND | 14 | https://www.molex.com/pdm_docs/sd/475900001_sd.pdf |  | N/A |  | Active | ROHS3 Compliant | 1 (Unlimited) | EAR99 | 8536.69.4040 | China | https://www.molex.com/datasheets/rohspdf/0475900001_rohs.pdf | WM17144CT-ND | REACH Unaffected | EACH | https://mm.digikey.com/Volume0/opasdata/d220001/medias/images/525/0475900001.JPG

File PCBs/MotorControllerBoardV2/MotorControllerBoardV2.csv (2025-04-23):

Reference | Qty | Value | DNP | Exclude from BOM | Exclude from Board | Footprint | Datasheet
C1,C5,C13,C14 | 4 | 100nF |  |  |  | Capacitor_THT:C_Disc_D3.0mm_W2.0mm_P2.50mm
C2,C3,C6,C7,C9,C12,C15 | 7 | 1μF |  |  |  | Capacitor_THT:C_Disc_D3.0mm_W2.0mm_P2.50mm
C4,C10 | 2 | 1nF |  |  |  | Capacitor_THT:C_Disc_D3.0mm_W2.0mm_P2.50mm
C8,C11 | 2 | 220μF |  |  |  | Capacitor_THT:C_Disc_D3.0mm_W2.0mm_P2.50mm
D1,D2,D3,D4,D5,D6,D7,D8,D9,D10,D11,D12,D13,D14,D15,D16 | 16 | B340-13-F |  |  |  | B340-13-F:DIO_B340-13-F
J1 | 1 | 2125201006 |  |  |  | 2125201006:MOLEX_2125201006
MLB1,MLF1,MRB1,MRF1 | 4 | Screw_Terminal_2_P5.00mm |  |  |  | TerminalBlock_Phoenix:TerminalBlock_Phoenix_PT-1,5-2-5.0-H_1x02_P5.00mm_Horizontal
R1,R2 | 2 | 54.5k |  |  |  | Resistor_THT:R_Axial_DIN0207_L6.3mm_D2.5mm_P5.08mm_Vertical
R3 | 1 | 1.2k |  |  |  | Resistor_THT:R_Axial_DIN0207_L6.3mm_D2.5mm_P5.08mm_Vertical
SW1 | 1 | SW_Push |  |  |  | Button_Switch_THT:SW_PUSH_6mm | ~
U1 | 1 | AVR128DB28x-xSP |  |  |  | Package_DIP:DIP-28_W7.62mm_Socket | https://ww1.microchip.com/downloads/en/DeviceDoc/AVR128DB28-32-48-64-DataSheet-DS40002247A.pdf
U2,U5 | 2 | L298N |  |  |  | L298N:Multiwatt15L V with heatsink v2 | http://www.st.com/st-web-ui/static/active/en/resource/technical/document/datasheet/CD00000240.pdf
U3,U4 | 2 | TCKE812NA_RF |  |  |  | TCKE812NA_RF:IC_TCKE812NA_RF
UPDIHeader1 | 1 | PINHD_1x3_Male |  |  |  | Connector_PinHeader_2.54mm:PinHeader_1x03_P2.54mm_Vertical

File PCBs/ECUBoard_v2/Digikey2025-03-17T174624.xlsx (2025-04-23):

Index | Quantity | Part Number | Manufacturer Part Number | Description | Customer Reference | Available | Backorder | Unit Price | Extended Price CAD
1 | 1 | 401-2001-ND | JS202011CQN | SWITCH SLIDE DPDT 300MA 6V | vp | 1 | 0 | 1.08 | 1.08
2 | 2 | 497-15484-1-ND | STS5P3LLH6 | MOSFET P-CH 30V 5A 8SO | vp | 2 | 0 | 1.7 | 3.40
3 | 3 | 296-LM25085MYX/NOPBCT-ND | LM25085MYX/NOPB | IC REG CTRLR BUCK 8MSOP | vp | 3 | 0 | 3.01 | 9.03
4 | 5 | 497-17240-1-ND | LDL1117S50R | IC REG LINEAR 5V 1.2A SOT-223 | vp | 5 | 0 | 0.76 | 3.80
5 | 5 | 497-17239-1-ND | LDL1117S33R | IC REG LINEAR 3.3V 1.2A SOT-223 | vp | 5 | 0 | 1.2 | 6.00
6 | 10 | 408-RG2012P-105-B-T5CT-ND | RG2012P-105-B-T5 | RES SMD 1M OHM 0.1% 1/8W 0805 | vp | 10 | 0 | 0.173 | 1.73
7 | 15 | RMCF0805FT3K92CT-ND | RMCF0805FT3K92 | RES 3.92K OHM 1% 1/8W 0805 | vp | 15 | 0 | 0.041 | 0.62
8 | 32 | B340-FDICT-ND | B340-13-F | DIODE SCHOTTKY 40V 3A SMC | vp | 32 | 0 | 0.296 | 9.47
9 | 4 | 264-TCKE812NARFCT-ND | TCKE812NA,RF | IC ELECTRONIC FUSE 10WSON | vp | 4 | 0 | 3.86 | 15.44
10 | 10 | RMCF0805FT18K7CT-ND | RMCF0805FT18K7 | RES 18.7K OHM 1% 1/8W 0805 | vp | 10 | 0 | 0.041 | 0.41
11 | 2 | A106657-ND | 215307-4 | CONN RCPT 8POS 0.1 GOLD PCB | vp | 2 | 0 | 1.9 | 3.80
12 | 10 | 541-41.2KCCT-ND | CRCW080541K2FKEA | RES SMD 41.2K OHM 1% 1/8W 0805 | vp | 10 | 0 | 0.068 | 0.68
13 | 4 | 900-2125201006-ND | 2125201006 | MINI-FIT MAX 6CKT HDR VERT | vp | 4 | 0 | 3.3 | 13.20
14 | 10 | 13-RT0805BRD07142KLCT-ND | RT0805BRD07142KL | RES 142K OHM 0.1% 1/8W 0805 | vp | 10 | 0 | 0.133 | 1.33
15 | 10 | 311-1.40KCRCT-ND | RC0805FR-071K4L | RES 1.4K OHM 1% 1/8W 0805 | vp | 10 | 0 | 0.015 | 0.15
16 | 2 | P124404CT-ND | ERJ-6CWDR013V | RES 0.013 OHM 0.5% 1/2W 0805 | vp | 2 | 0 | 1 | 2.00
17 | 3 | 296-47233-1-ND | TPS259251DRCR | IC ELECTRONIC FUSE 15% 10VSON | vp | 3 | 0 | 2.25 | 6.75
18 | 20 | RMCF0805FT330RCT-ND | RMCF0805FT330R | RES 330 OHM 1% 1/8W 0805 | vp | 20 | 0 | 0.041 | 0.82
19 | 2 | 553-3445-1-ND | PA4343.133NLT | FIXED IND 13UH 9A 24 MOHM SMD | vp | 2 | 0 | 2.43 | 4.86
20 | 10 | 160-1436-1-ND | LTST-C190KRKT | LED RED CLEAR CHIP SMD | vp | 10 | 0 | 0.152 | 1.52
21 | 4 | SK54A-LTPMSCT-ND | SK54A-LTP | DIODE SCHOTTKY 40V 5A DO214AC | vp | 4 | 0 | 0.49 | 1.96
22 | 10 | 846-SML-D12P8WT86CT-ND | SML-D12P8WT86 | LED GREEN DIFFUSED 1608 SMD | vp | 10 | 0 | 0.152 | 1.52
23 | 10 | 1276-CL21A226MAYNNNECT-ND | CL21A226MAYNNNE | CAP CER 22UF 25V X5R 0805 | vp | 10 | 0 | 0.158 | 1.58
24 | 10 | 311-1132-1-ND | CC0805KRX7R9BB392 | CAP CER 3900PF 50V X7R 0805 | vp | 10 | 0 | 0.1 | 1.00
25 | 10 | 1276-1244-1-ND | CL21A475KAQNNNE | CAP CER 4.7UF 25V X5R 0805 | vp | 10 | 0 | 0.087 | 0.87
26 | 3 | 493-2225-1-ND | UWT1H470MCL1GS | CAP ALUM 47UF 20% 50V SMD | vp | 3 | 0 | 0.64 | 1.92
27 | 10 | 490-3328-1-ND | GRM21BR71H474KA88L | CAP CER 0.47UF 50V X7R 0805 | vp | 10 | 0 | 0.19 | 1.90
28 | 10 | 1276-1029-1-ND | CL21B105KBFNNNE | CAP CER 1UF 50V X7R 0805 | vp | 10 | 0 | 0.062 | 0.62
29 | 10 | 399-C0805C102K5RACTUCT-ND | C0805C102K5RACTU | CAP CER 1000PF 50V X7R 0805 | vp | 10 | 0 | 0.138 | 1.38
30 | 10 | 311-1140-1-ND | CC0805KRX7R9BB104 | CAP CER 0.1UF 50V X7R 0805 | vp | 10 | 0 | 0.052 | 0.52
31 | 5 | 296-47192-ND | LM7805CT/NOPB | IC REG LINEAR 5V 1.5A TO220-3 | ik | 5 | 0 | 2.82 | 14.10
32 | 32 | SB220-E3/54GICT-ND | SB220-E3/54 | DIODE SCHOTTKY 20V 2A DO204AC | ik | 32 | 0 | 0.482 | 15.42
33 | 20 | 277-1667-ND | 1935161 | TERM BLK 2POS SIDE ENTRY 5MM PCB | vp | 20 | 0 | 0.59 | 11.80
34 | 10 | 102-1153-ND | CEM-1203(42) | BUZZER MAGNETIC 3.5V 12.00MM TH | ik | 10 | 0 | 0.872 | 8.72
35 | 4 | 900-2125141006-ND | 2125141006 | CONN RCPT HSG 6POS 4.20MM | vp | 4 | 0 | 1.59 | 6.36
36 | 25 | 900-2125153101CT-ND | 2125153101 | MINI-FIT MAX 14AWG RECEPT TML TI | vp | 25 | 0 | 0.2188 | 5.47
37 | 5 | LM555CNNS/NOPB-ND | LM555CN/NOPB | IC OSC SINGLE TIMER 100KHZ 8-DIP | ik | 5 | 0 | 1.86 | 9.30

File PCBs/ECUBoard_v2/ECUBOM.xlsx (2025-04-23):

Line # | Name | Description | Designator | Quantity | Supplier Part Number | Manufacturer Part Number | Revision ID | Revision State | Revision Status | Manufacturer 1 | Manufacturer Part Number 1 | Manufacturer Lifecycle 1 | Supplier 1 | Supplier Part Number 1 | Supplier Unit Price 1 | Supplier Subtotal 1
 | 1uF | Ceramic Capacitor, Multilayer, Ceramic, 50V, 10% +Tol, 10% -Tol, X7R, 15% TC, 1uF, Surface Mount, 0805 | 20, C1, C2, C4, C5, C10, C19 | 7 | 1276-1029-1-ND | CL21B105KBFNNNE |  | Not managed
 | 0.1uF | Ceramic Capacitor, Multilayer, Ceramic, 50V, 10% +Tol, 10% -Tol, X7R, 15% TC, 0.1uF, Surface Mount, 0805 | C3, C7, C14, C15, C16 | 5 | 311-1140-1-ND | CC0805KRX7R9BB104 |  | Not managed
 | 0.47uF | Ceramic Capacitor, Multilayer, Ceramic, 50V, 10% +Tol, 10% -Tol, X7R, 15% TC, 0.47uF, Surface Mount, 0805 | C8 | 1 | 81-GRM21BR71H474KA88 | GRM21BR71H474KA88L |  | Not managed
 | 1000pF | Ceramic Capacitor, Multilayer, Ceramic, 50V, 10% +Tol, 10% -Tol, X7R, 15% TC, 0.001uF, Surface Mount, 0805 | C9 | 1 | C0805C102K5RACTU | C0805C102K5RACTU |  | Not managed
 | 47uF | Aluminum Electrolytic Capacitor, Polarized, Aluminum (wet), 50V, 20% +Tol, 20% -Tol, 47uF, Surface Mount, 2626 | C11 | 1 | 493-2225-1-ND | UWT1H470MCL1GS |  | Not managed
 | 3.9nF | Ceramic Capacitor, Multilayer, Ceramic, 50V, 10% +Tol, 10% -Tol, X7R, 15% TC, 0.0039uF, Surface Mount, 0805 | C12 | 1 | 311-1132-1-ND | CC0805KRX7R9BB392 |  | Not managed
 | 22uF | Ceramic Capacitor, Multilayer, Ceramic, 25V, 20% +Tol, 20% -Tol, X5R, 15% TC, 22uF, Surface Mount, 0805 | C13 | 1 | 1276-CL21A226MAYNNNECT-ND | CL21A226MAYNNNE |  | Not managed
 | 4.7uF | Ceramic Capacitor, Multilayer, Ceramic, 25V, 10% +Tol, 10% -Tol, X5R, 15% TC, 4.7uF, Surface Mount, 0805 | C17, C18 | 2 | 1276-1244-1-ND | CL21A475KAQNNNE |  | Not managed
 | redSML-D12U1WT86 | Single Color LED, Red, Milky White, 1.2mm | D1 | 1 | SML-D12U1WT86CT-ND | SML-D12U1WT86 |  | Not managed
 | greenSML-D12P8WT86 | Single Color LED, Pure Green, Diffused Milky White, 1.2mm | D2 | 1 | 846-SML-D12P8WT86CT-ND | SML-D12P8WT86 |  | Not managed
 | 40V 5A | Rectifier Diode, Schottky, 1 Phase, 1 Element, 5A, 40V V(RRM), Silicon, DO-214AC | D3 | 1 | SK54A-LTPMSCT-ND | SK54A-LTP |  | Not managed
 | FUSE TPS259251DRCR | Power Supply Support Circuit, Adjustable, 1 Channel, PDSO10 | F1 | 1 | 296-47233-1-ND | TPS259251DRCR |  | Not managed
 | Molex2125201006 | Connector Power Header 6 Position 4.2mm Solder Through Hole Tray | J1, J4 | 2 | 212520-1006 | 212520-1006 |  | Not managed
 | 8pos215307-4 | Board Connector, 4 Contact(s), 2 Row(s), Female, Straight, 0.1 inch Pitch, Solder Terminal, Black Insulator, Receptacle | J2 | 1 | 98K6517 | 215307-4 |  | Not managed
 | ScrewTwo1984617 | Barrier Strip Terminal Block, 17.5A, 1.5mm2, 1 Row(s), 1 Deck(s) | J3, J6, J7, J8, J9, J10 | 6 | 277-1721-ND | 1984617 |  | Not managed
 | Pos3Header1945106 | Board Connector, 3 Contact(s), 1 Row(s), Male, Straight, Solder Terminal, Black Insulator | J5 | 1 | 277-1750-ND | PST1,0/3-3,5 |  | Not managed
 | 13uH | General Purpose Inductor, 13uH, 20%, 1 Element, SMD, 5550 | L1 | 1 | 553-3445-1-ND | PA4343.133NLT |  | Not managed
 | BuzzerCEM-120342 | Audio Signaling/Alarm Devices | LS1 | 1 | CEM-1203(42) | CEM-1203(42) |  | Not managed
 | 330 | Fixed Resistor, Metal Glaze/thick Film, 0.125W, 330ohm, 150V, 1% +/-Tol, 100ppm/Cel, Surface Mount, 0805 | R2, R3, R5, R6, R7, R8, R9, R10 | 8 | RMCF0805FT330RCT-ND | RMCF0805FT330R |  | Not managed
 | 1.4k | Fixed Resistor, Metal Glaze/thick Film, 0.125W, 1400ohm, 150V, 1% +/-Tol, 100ppm/Cel, Surface Mount, 0805 | R4, R11 | 2 | 5205166 | RC0805FR-071K4L |  | Not managed
 | 142K | Fixed Resistor, Thin Film, 0.125W, 142000ohm, 150V, 0.1% +/-Tol, 25ppm/Cel, Surface Mount, 0805 | R12, R22 | 2 | 13-RT0805BRD07142KLCT-ND | RT0805BRD07142KL |  | Not managed
 | 13m | Resistor Thick Film 0.013Ohm 0.5% 0.5W 2-Pin 0805 T/R | R13 | 1 | 667-ERJ-6CWDR013V | ERJ-6CWDR013V |  | Not managed
 | 41.2k | Fixed Resistor, Metal Glaze/thick Film, 0.125W, 41200ohm, 150V, 1% +/-Tol, 100ppm/Cel, Surface Mount, 0805 | R14 | 1 | CRCW080541K2FKEA | CRCW080541K2FKEA |  | Not managed
 | 18.7k | Fixed Resistor, Metal Glaze/thick Film, 0.125W, 18700ohm, 150V, 1% +/-Tol, 100ppm/Cel, Surface Mount, 0805 | R15, R18 | 2 | RMCF0805FT18K7CT-ND | RMCF0805FT18K7 |  | Not managed
 | 3.9k | Fixed Resistor, Metal Glaze/thick Film, 0.125W, 3920ohm, 150V, 1% +/-Tol, 100ppm/Cel, Surface Mount, 0805 | R16, R17 | 2 | RMCF0805FT3K92CT-ND | RMCF0805FT3K92 |  | Not managed
 | 41.2K | Fixed Resistor, Metal Glaze/thick Film, 0.125W, 41200ohm, 150V, 1% +/-Tol, 100ppm/Cel, Surface Mount, 0805 | R19, R20 | 2 | CRCW080541K2FKEA | CRCW080541K2FKEA |  | Not managed
 | 1M | Fixed Resistor, Thin Film, 0.125W, 1000000ohm, 150V, 0.1% +/-Tol, 10ppm/Cel, Surface Mount, 0805 | R21 | 1 | 541-TNPW08051M00BYEACT-ND | TNPW08051M00BYEA |  | Not managed
 | SWT JS202011CQN | Slide Switch, 1 Positions, DPDT, Latched, 0.3A, 6VDC, 6 PCB Hole Cnt, Solder Terminal, Through Hole-straight | SW1 | 1 | 401-2001-ND | JS202011CQN |  | Not managed
 | Button1825910-6 | Keypad Switch, 1 Switches, SPST, Momentary-tactile, 0.05A, 24VDC, 2.06N, 4 PCB Hole Cnt, Solder Terminal, Through Hole-straight | SW2 | 1 | 1825910-6 | 1825910-6 |  | Not managed
 | AVR128DB28-I/SP | RISC Microcontroller, 8-Bit, FLASH, AVR CPU, 24MHz, CMOS, PDIP28 | U1 | 1 | 12AJ7043 | AVR128DB28-I/SP |  | Not managed
 | PfetSTS5P3LLH6 | Power Field-Effect Transistor, 5A I(D), 1-Element, P-Channel, Metal-oxide Semiconductor FET | U2 | 1 | STS5P3LLH6 | STS5P3LLH6 |  | Not managed
 | IC BUCK LM25085MYX/NOPB | Switching Controller, Voltage-mode, 10A, 1000kHz Switching Freq-Max, PDSO8 | U3 | 1 | 296-LM25085MYX/NOPBCT-ND | LM25085MYX/NOPB |  | Not managed
 | LDL1117S50R | Fixed Positive LDO Regulator, 5V, 0.6V Dropout, PDSO4 | U4 | 1 | LDL1117S50R | LDL1117S50R |  | Not managed
 | LDL1117S33R | Fixed Positive LDO Regulator, 3.3V, 0.6V Dropout, PDSO4 | U5 | 1 | LDL1117S33R | LDL1117S33R |  | Not managed |  |  |  |  | Arrow Electronics | LDL1117S33R

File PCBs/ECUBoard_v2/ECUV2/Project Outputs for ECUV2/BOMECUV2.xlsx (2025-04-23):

Line # | Comment | Description | Designator | Quantity | Manufacturer | Manufacturer Part Number | Supplier | Supplier Part Number
 | 300mA | 12.7 x 7.5 x 4.5 mm, 2 mm Raised Slide Actuator, Right Angle, Through Hole, Slide Switch | SW2 | 1 | Same Sky | SLW-1277545-2A-RA-S-D | Digikey | 2223-SLW-1277545-2A-RA-S-D-ND
 | 47uF | Aluminum Electrolytic Capacitor, Polarized, Aluminum (wet), 50V, 20% +Tol, 20% -Tol, 47uF, Surface Mount, 2626 | C8 | 1 | Nichicon | UWT1H470MCL1GS | Digikey | 493-2225-1-ND
 | 47uF | Aluminum Electrolytic Capacitor, Polarized, Aluminum (wet), 50V, 20% +Tol, 20% -Tol, 47uF, Surface Mount, 2626 | C9 | 1 | Nichicon | UWT1H470MCL1GS | Digikey | 493-2225-1-ND
 | BuzzerCEM-120342 | Audio Signaling/Alarm Devices | LS1 | 1 | CUI Devices | CEM-1203(42) | Arrow Electronics | CEM-1203(42)
 | 2.54mm | Barrier Strip Terminal Block, 6A, 1 Row(s), 1 Deck(s) | J5 | 1 | On-Shore Technology | OSTVN02A150 | Digikey | ED10561-ND
 | 2.54mm | Barrier Strip Terminal Block, 6A, 1 Row(s), 1 Deck(s) | J6 | 1 | On-Shore Technology | OSTVN02A150 | Digikey | ED10561-ND
 | 2.54mm | Barrier Strip Terminal Block, 6A, 1 Row(s), 1 Deck(s) | J7 | 1 | On-Shore Technology | OSTVN02A150 | Digikey | ED10561-ND
 | 2.54mm | Barrier Strip Terminal Block, 6A, 1 Row(s), 1 Deck(s) | J8 | 1 | On-Shore Technology | OSTVN02A150 | Digikey | ED10561-ND
 | 2.54mm | Barrier Strip Terminal Block, 6A, 1 Row(s), 1 Deck(s) | J10 | 1 | On-Shore Technology | OSTVN02A150 | Digikey | ED10561-ND
 | 2.54mm | Barrier Strip Terminal Block, 6A, 1 Row(s), 1 Deck(s) | J11 | 1 | On-Shore Technology | OSTVN02A150 | Digikey | ED10561-ND
 | 2.54mm | Barrier Strip Terminal Block, 6A, 1 Row(s), 1 Deck(s) | J12 | 1 | On-Shore Technology | OSTVN02A150 | Digikey | ED10561-ND
 | 8pos215307-4 | Board Connector, 4 Contact(s), 2 Row(s), Female, Straight, 0.1 inch Pitch, Solder Terminal, Black Insulator, Receptacle | J2 | 1 | TE Connectivity | 215307-4 | Avnet | 98K6517
 | 2.54mm | Board Connector, 38 Contact(s), 1 Row(s), Male, Straight, 0.1 inch Pitch, Solder Terminal, Black Insulator | J4 | 1 | Samtec | TS-103-T-A | Digikey | SAM1112-03-ND
 | 4.7uF | Ceramic Capacitor, Multilayer, Ceramic, 25V, 10% +Tol, 10% -Tol, X5R, 15% TC, 4.7uF, Surface Mount, 0805 | C10 | 1 | Samsung | CL21A475KAQNNNE | Digikey | 1276-1244-1-ND
 | 4.7uF | Ceramic Capacitor, Multilayer, Ceramic, 25V, 10% +Tol, 10% -Tol, X5R, 15% TC, 4.7uF, Surface Mount, 0805 | C11 | 1 | Samsung | CL21A475KAQNNNE | Digikey | 1276-1244-1-ND
 | 0.1uF | Ceramic Capacitor, Multilayer, Ceramic, 50V, 10% +Tol, 10% -Tol, X7R, 15% TC, 0.1uF, Surface Mount, 0805 | C3 | 1 | Yageo | CC0805KRX7R9BB104 | Digikey | 311-1140-1-ND
 | 0.1uF | Ceramic Capacitor, Multilayer, Ceramic, 50V, 10% +Tol, 10% -Tol, X7R, 15% TC, 0.1uF, Surface Mount, 0805 | C6 | 1 | Yageo | CC0805KRX7R9BB104 | Digikey | 311-1140-1-ND
 | 0.1uF | Ceramic Capacitor, Multilayer, Ceramic, 50V, 10% +Tol, 10% -Tol, X7R, 15% TC, 0.1uF, Surface Mount, 0805 | C7 | 1 | Yageo | CC0805KRX7R9BB104 | Digikey | 311-1140-1-ND
 | 1uF | Ceramic Capacitor, Multilayer, Ceramic, 50V, 10% +Tol, 10% -Tol, X7R, 15% TC, 1uF, Surface Mount, 0805 | C1 | 1 | Samsung | CL21B105KBFNNNE | Digikey | 1276-1029-1-ND
 | 1uF | Ceramic Capacitor, Multilayer, Ceramic, 50V, 10% +Tol, 10% -Tol, X7R, 15% TC, 1uF, Surface Mount, 0805 | C2 | 1 | Samsung | CL21B105KBFNNNE | Digikey | 1276-1029-1-ND
 | 1uF | Ceramic Capacitor, Multilayer, Ceramic, 50V, 10% +Tol, 10% -Tol, X7R, 15% TC, 1uF, Surface Mount, 0805 | C4 | 1 | Samsung | CL21B105KBFNNNE | Digikey | 1276-1029-1-ND
 | 1uF | Ceramic Capacitor, Multilayer, Ceramic, 50V, 10% +Tol, 10% -Tol, X7R, 15% TC, 1uF, Surface Mount, 0805 | C5 | 1 | Samsung | CL21B105KBFNNNE | Digikey | 1276-1029-1-ND
 | 1uF | Ceramic Capacitor, Multilayer, Ceramic, 50V, 10% +Tol, 10% -Tol, X7R, 15% TC, 1uF, Surface Mount, 0805 | C12 | 1 | Samsung | CL21B105KBFNNNE | Digikey | 1276-1029-1-ND
 | 1uF | Ceramic Capacitor, Multilayer, Ceramic, 50V, 10% +Tol, 10% -Tol, X7R, 15% TC, 1uF, Surface Mount, 0805 | C13 | 1 | Samsung | CL21B105KBFNNNE | Digikey | 1276-1029-1-ND
 | Molex2125201006 | Connector Power Header 6 Position 4.2mm Solder Through Hole Tray | J1 | 1 | Molex | 212520-1006 | Arrow Electronics | 212520-1006
 | Molex2125201006 | Connector Power Header 6 Position 4.2mm Solder Through Hole Tray | J3 | 1 | Molex | 212520-1006 | Arrow Electronics | 212520-1006
 | LDL1117S33R | Fixed Positive LDO Regulator, 3.3V, 0.6V Dropout, PDSO4 | U2 | 1 | STMicroelectronics | LDL1117S33R | Arrow Electronics | LDL1117S33R
 | LDL1117S50R | Fixed Positive LDO Regulator, 5V, 0.6V Dropout, PDSO4 | U3 | 1 | STMicroelectronics | LDL1117S50R | Arrow Electronics | LDL1117S50R
 | 150 | Fixed Resistor, Metal Glaze/thick Film, 0.125W, 150ohm, 150V, 1% +/-Tol, 100ppm/Cel, Surface Mount, 0805 | R3 | 1 | Yageo | RC0805FR-07150RL | Digikey | 311-150CRCT-ND
 | 150 | Fixed Resistor, Metal Glaze/thick Film, 0.125W, 150ohm, 150V, 1% +/-Tol, 100ppm/Cel, Surface Mount, 0805 | R4 | 1 | Yageo | RC0805FR-07150RL | Digikey | 311-150CRCT-ND
 | 150 | Fixed Resistor, Metal Glaze/thick Film, 0.125W, 150ohm, 150V, 1% +/-Tol, 100ppm/Cel, Surface Mount, 0805 | R6 | 1 | Yageo | RC0805FR-07150RL | Digikey | 311-150CRCT-ND
 | 150 | Fixed Resistor, Metal Glaze/thick Film, 0.125W, 150ohm, 150V, 1% +/-Tol, 100ppm/Cel, Surface Mount, 0805 | R13 | 1 | Yageo | RC0805FR-07150RL | Digikey | 311-150CRCT-ND
 | 150 | Fixed Resistor, Metal Glaze/thick Film, 0.125W, 150ohm, 150V, 1% +/-Tol, 100ppm/Cel, Surface Mount, 0805 | R14 | 1 | Yageo | RC0805FR-07150RL | Digikey | 311-150CRCT-ND
 | 150 | Fixed Resistor, Metal Glaze/thick Film, 0.125W, 150ohm, 150V, 1% +/-Tol, 100ppm/Cel, Surface Mount, 0805 | R16 | 1 | Yageo | RC0805FR-07150RL | Digikey | 311-150CRCT-ND
 | 150 | Fixed Resistor, Metal Glaze/thick Film, 0.125W, 150ohm, 150V, 1% +/-Tol, 100ppm/Cel, Surface Mount, 0805 | R17 | 1 | Yageo | RC0805FR-07150RL | Digikey | 311-150CRCT-ND
 | 150 | Fixed Resistor, Metal Glaze/thick Film, 0.125W, 150ohm, 150V, 1% +/-Tol, 100ppm/Cel, Surface Mount, 0805 | R18 | 1 | Yageo | RC0805FR-07150RL | Digikey | 311-150CRCT-ND
 | 150 | Fixed Resistor, Metal Glaze/thick Film, 0.125W, 150ohm, 150V, 1% +/-Tol, 100ppm/Cel, Surface Mount, 0805 | R19 | 1 | Yageo | RC0805FR-07150RL | Digikey | 311-150CRCT-ND
 | 330 | Fixed Resistor, Metal Glaze/thick Film, 0.125W, 330ohm, 150V, 1% +/-Tol, 100ppm/Cel, Surface Mount, 0805 | R11 | 1 | Stackpole Electronics | RMCF0805FT330R | Digikey | RMCF0805FT330RCT-ND
 | 1.4k | Fixed Resistor, Metal Glaze/thick Film, 0.125W, 1400ohm, 150V, 1% +/-Tol, 100ppm/Cel, Surface Mount, 0805 | R5 | 1 | Yageo | RC0805FR-071K4L | Future Electronics | 5205166
 | 1.4k | Fixed Resistor, Metal Glaze/thick Film, 0.125W, 1400ohm, 150V, 1% +/-Tol, 100ppm/Cel, Surface Mount, 0805 | R20 | 1 | Yageo | RC0805FR-071K4L | Future Electronics | 5205166
 | 3.9k | Fixed Resistor, Metal Glaze/thick Film, 0.125W, 3920ohm, 150V, 1% +/-Tol, 100ppm/Cel, Surface Mount, 0805 | R1 | 1 | Stackpole Electronics | RMCF0805FT3K92 | Digikey | RMCF0805FT3K92CT-ND
 | 3.9k | Fixed Resistor, Metal Glaze/thick Film, 0.125W, 3920ohm, 150V, 1% +/-Tol, 100ppm/Cel, Surface Mount, 0805 | R2 | 1 | Stackpole Electronics | RMCF0805FT3K92 | Digikey | RMCF0805FT3K92CT-ND
 | 3.9k | Fixed Resistor, Metal Glaze/thick Film, 0.125W, 3920ohm, 150V, 1% +/-Tol, 100ppm/Cel, Surface Mount, 0805 | R7 | 1 | Stackpole Electronics | RMCF0805FT3K92 | Digikey | RMCF0805FT3K92CT-ND
 | 10k | Fixed Resistor, Metal Glaze/thick Film, 0.125W, 10000ohm, 150V, 1% +/-Tol, 100ppm/Cel, Surface Mount, 0805 | R8 | 1 | Stackpole Electronics | RMCF0805FT10K0 | Digikey | RMCF0805FT10K0CT-ND
 | 10k | Fixed Resistor, Metal Glaze/thick Film, 0.125W, 10000ohm, 150V, 1% +/-Tol, 100ppm/Cel, Surface Mount, 0805 | R15 | 1 | Stackpole Electronics | RMCF0805FT10K0 | Digikey | RMCF0805FT10K0CT-ND
 | 18.7k | Fixed Resistor, Metal Glaze/thick Film, 0.125W, 18700ohm, 150V, 1% +/-Tol, 100ppm/Cel, Surface Mount, 0805 | R9 | 1 | Stackpole Electronics | RMCF0805FT18K7 | Digikey | RMCF0805FT18K7CT-ND
 | 41.2K | Fixed Resistor, Metal Glaze/thick Film, 0.125W, 41200ohm, 150V, 1% +/-Tol, 100ppm/Cel, Surface Mount, 0805 | R10 | 1 | Vishay | CRCW080541K2FKEA | Arrow Electronics | CRCW080541K2FKEA
 | 41.2K | Fixed Resistor, Metal Glaze/thick Film, 0.125W, 41200ohm, 150V, 1% +/-Tol, 100ppm/Cel, Surface Mount, 0805 | R12 | 1 | Vishay | CRCW080541K2FKEA | Arrow Electronics | CRCW080541K2FKEA
 | Button1825910-6 | Keypad Switch, 1 Switches, SPST, Momentary-tactile, 0.05A, 24VDC, 2.06N, 4 PCB Hole Cnt, Solder Terminal, Through Hole-straight | SW1 | 1 | TE Connectivity Alcoswitch | 1825910-6 | Avnet | 1825910-6
 | 6A | Power Field-Effect Transistor, 6A I(D), 30V, 0.042ohm, 1-Element, P-Channel, Silicon, Metal-oxide Semiconductor FET | PMOS1 | 1 | Toshiba | SSM3J372R,LF | Digikey | SSM3J372RLFCT-ND
 | 6A | Power Field-Effect Transistor, 6A I(D), 30V, 0.042ohm, 1-Element, P-Channel, Silicon, Metal-oxide Semiconductor FET | PMOS2 | 1 | Toshiba | SSM3J372R,LF | Digikey | SSM3J372RLFCT-ND
 | AVR128DB28-I/SP | RISC Microcontroller, 8-Bit, FLASH, AVR CPU, 24MHz, CMOS, PDIP28 | U1 | 1 | Microchip | AVR128DB28-I/SP | Newark | 12AJ7043
 | green | Single Color LED, Pure Green, Diffused Milky White, 1.2mm | D2 | 1 | Rohm | SML-D12P8WT86 | Digikey | 846-SML-D12P8WT86CT-ND
 | green | Single Color LED, Pure Green, Diffused Milky White, 1.2mm | D3 | 1 | Rohm | SML-D12P8WT86 | Digikey | 846-SML-D12P8WT86CT-ND
 | green | Single Color LED, Pure Green, Diffused Milky White, 1.2mm | D4 | 1 | Rohm | SML-D12P8WT86 | Digikey | 846-SML-D12P8WT86CT-ND
 | green | Single Color LED, Pure Green, Diffused Milky White, 1.2mm | D5 | 1 | Rohm | SML-D12P8WT86 | Digikey | 846-SML-D12P8WT86CT-ND
 | red | Single Color LED, Red, Diffused Milky White, 1.2mm | D1 | 1 | Rohm | SML-D12U1WT86 | Digikey | SML-D12U1WT86CT-ND
 | TP | Testing/Accessories | TP1 | 1 | KOA Speer | RCTCTE | Digikey | 2019-RCTCTECT-ND
 | TP | Testing/Accessories | TP2 | 1 | KOA Speer | RCTCTE | Digikey | 2019-RCTCTECT-ND
 | TP | Testing/Accessories | TP3 | 1 | KOA Speer | RCTCTE | Digikey | 2019-RCTCTECT-ND
 | TP | Testing/Accessories | TP4 | 1 | KOA Speer | RCTCTE | Digikey | 2019-RCTCTECT-ND
 | TP | Testing/Accessories | TP5 | 1 | KOA Speer | RCTCTE | Digikey | 2019-RCTCTECT-ND
 | TP | Testing/Accessories | TP6 | 1 | KOA Speer | RCTCTE | Digikey | 2019-RCTCTECT-ND
 | TP | Testing/Accessories | TP7 | 1 | KOA Speer | RCTCTE | Digikey | 2019-RCTCTECT-ND
 | TP | Testing/Accessories | TP8 | 1 | KOA Speer | RCTCTE | Digikey | 2019-RCTCTECT-ND
 | TP | Testing/Accessories | TP9 | 1 | KOA Speer | RCTCTE | Digikey | 2019-RCTCTECT-ND
 | TP | Testing/Accessories | TP10 | 1 | KOA Speer | RCTCTE | Digikey | 2019-RCTCTECT-ND
 | TP | Testing/Accessories | TP11 | 1 | KOA Speer | RCTCTE | Digikey | 2019-RCTCTECT-ND
 | TP | Testing/Accessories | TP12 | 1 | KOA Speer | RCTCTE | Digikey | 2019-RCTCTECT-ND
 | TP | Testing/Accessories | TP13 | 1 | KOA Speer | RCTCTE | Digikey | 2019-RCTCTECT-ND
 | TP | Testing/Accessories | TP14 | 1 | KOA Speer | RCTCTE | Digikey | 2019-RCTCTECT-ND
 | TP | Testing/Accessories | TP15 | 1 | KOA Speer | RCTCTE | Digikey | 2019-RCTCTECT-ND
 | micro ab | USB Connector, 5 Contact(s), Female, Right Angle, Surface Mount Terminal, Locking, Receptacle | J9 | 1 | Molex | 47590-0001 | Digikey | WM17144CT-ND

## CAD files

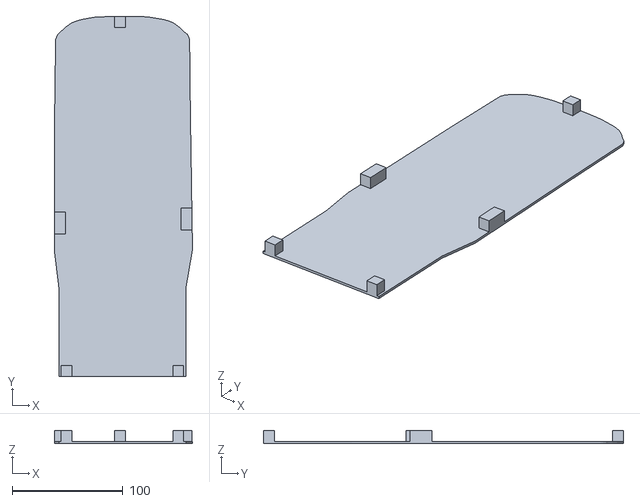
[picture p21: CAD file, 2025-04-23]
3dDesign/Body/dodge_base v7.stl
124.7 x 325.7 x 11.9

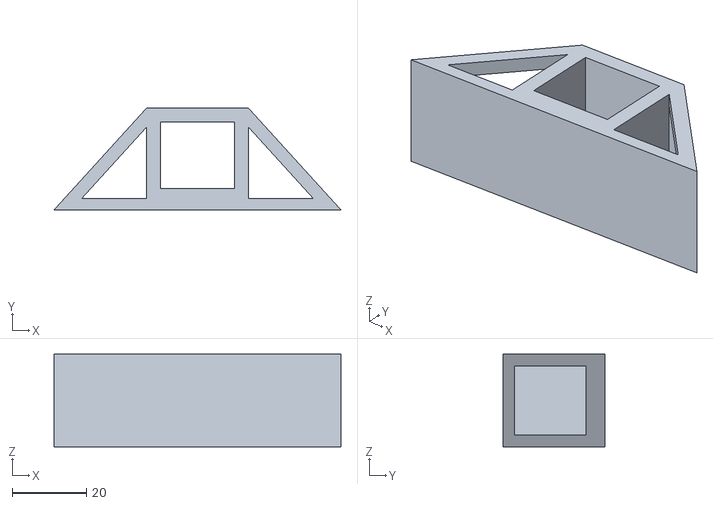
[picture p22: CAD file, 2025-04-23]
3dDesign/Misc/Motor_Base v12.stl
77.5 x 27.5 x 25.0

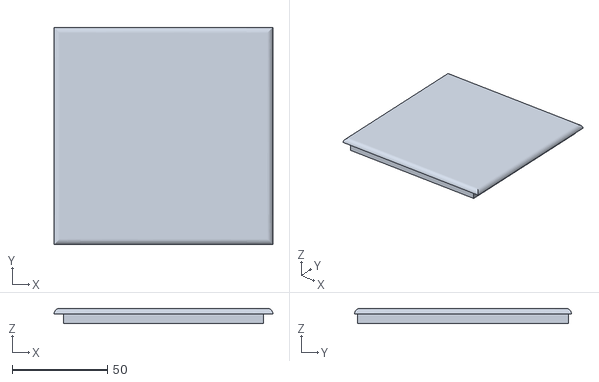
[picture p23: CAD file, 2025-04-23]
3dDesign/Body/Tonneau_Cover v1.stl
115.0 x 114.0 x 8.00

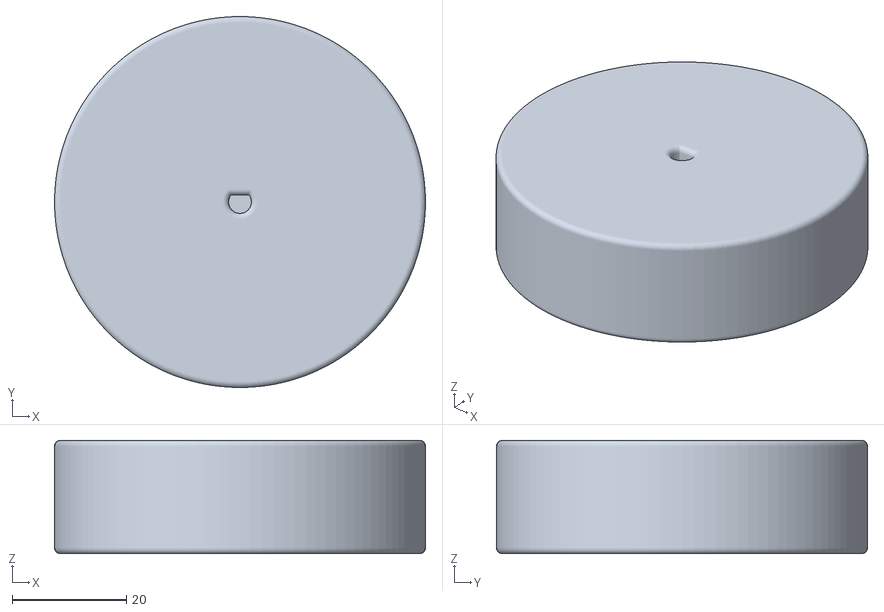
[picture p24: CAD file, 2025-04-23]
3dDesign/Misc/ENEL300_Tire_D_Type v1.stl
65.0 x 65.0 x 19.8

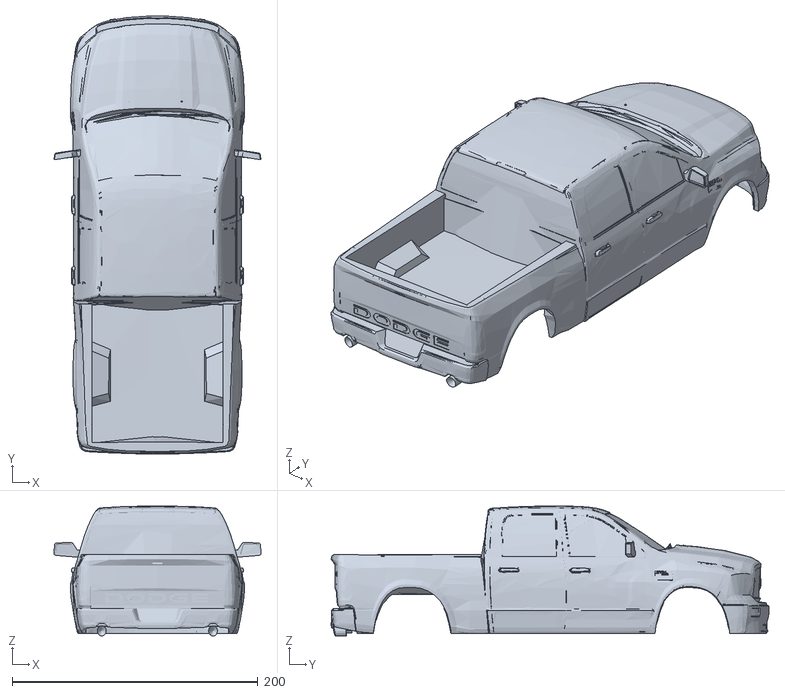
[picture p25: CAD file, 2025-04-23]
3dDesign/Body/dodge_chassis v6.stl
168.5 x 356.4 x 105.8

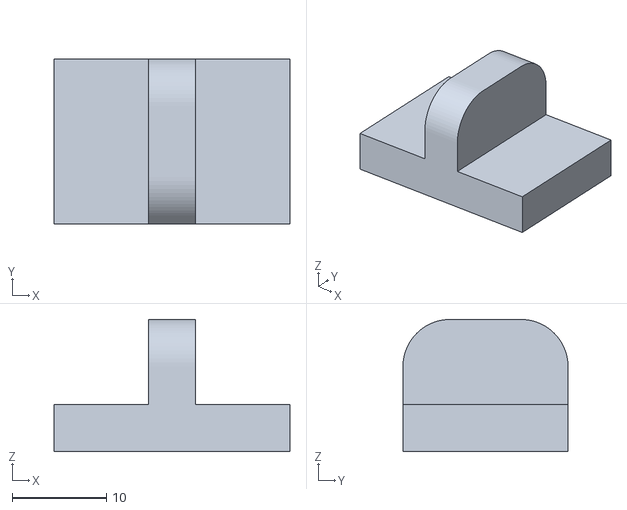
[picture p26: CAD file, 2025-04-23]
3dDesign/Misc/ENEL300_Motor_Bracket_T v4.stl
25.0 x 17.5 x 14.0

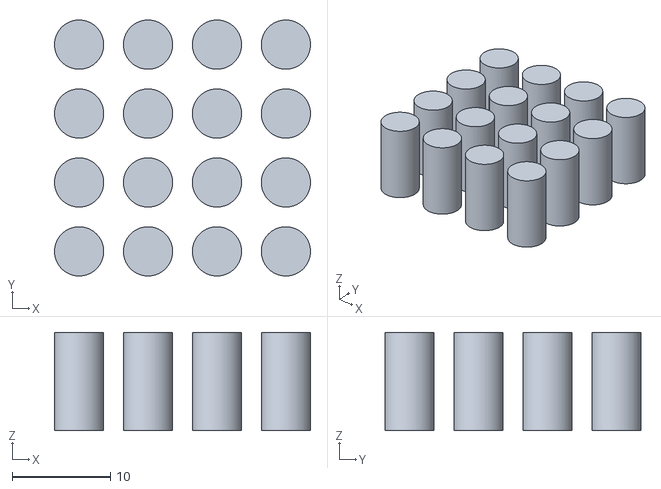
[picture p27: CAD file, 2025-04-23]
3dDesign/Misc/Standoffs_V1 v1.stl
26.0 x 26.0 x 10.0

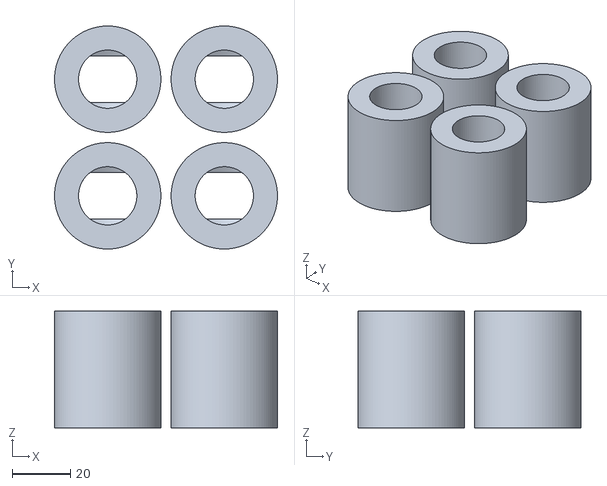
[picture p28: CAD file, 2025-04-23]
3dDesign/Misc/MotorMountAdaptersV1 v2.stl
76.5 x 76.5 x 40.0

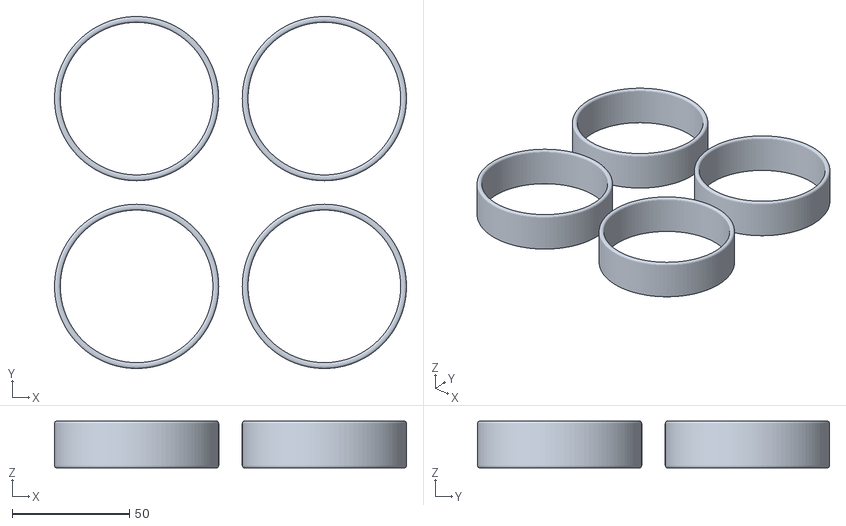
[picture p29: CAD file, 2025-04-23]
3dDesign/Misc/ENEL300_Tire_Outer_v1 v2.stl
150.0 x 150.0 x 20.0

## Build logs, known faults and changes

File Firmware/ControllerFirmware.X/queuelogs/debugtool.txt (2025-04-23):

1237 1745346738455 GEN4_TO_CONTROLLER_LOG:GEN4_PROGRAM_INT_LOG_AVR128DB28 Pre:endOfOperations
1237 1745346738455 GEN4_TO_CONTROLLER_LOG:GEN4_PROGRAM_INT_LOG_AVR128DB28 Payload
1237 1745346738455 GEN4_TO_CONTROLLER_LOG:GEN4_PROGRAM_INT_LOG_AVR128DB28 null
1237 1745346738455 GEN4_TO_CONTROLLER_LOG:GEN4_PROGRAM_INT_LOG_AVR128DB28 Payload End
1237 1745346738455 XXXX 1745346738455, Thread 1237: XXXX 1745346738455, Entering Thread 1237: Commands::runScriptBasic, script name = ExitProgMode, timeOut = -1 ms  
1237 1745346738456 XXXX 1745346738456, Thread 1237: com.Send returned false 
1237 1745346738456 XXXX 1745346738456, Thread 1237: transfer: exception after writeHeaderAndGetResult null 
1237 1745346738456 XXXX 1745346738456, Thread 1237: XXXX 1745346738456, Entering Thread 1237: ToolCommUsb::recoverFromProtocolError, type = NO_SCRIPT  
1237 1745346738456 XXXX 1745346738456, Thread 1237: Send Abort Script Engine Command 
1237 1745346738457 XXXX 1745346738457, Thread 1237: XXXX 1745346738456, Entering Thread 1237: ToolCommUsb::killScriptEngine  
1237 1745346738458 XXXX 1745346738458, Thread 1237: com.Send returned false 
1237 1745346738459 XXXX 1745346738459, Thread 1237: Failed sending Abort Script Engine Command. Set nuclear option = true 
1237 1745346738459 XXXX 1745346738459, Thread 1237: About to nuke 
1237 1745346738459 XXXX 1745346738459, Thread 1237: XXXX 1745346738459, Entering Thread 1237: ToolCommUsb::nuclearOption  
1237 1745346738460 XXXX 1745346738460, Thread 1237: com.Send returned false

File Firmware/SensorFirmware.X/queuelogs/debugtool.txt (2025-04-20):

394 1745177538494 GEN4_CONNECT_DIAGNOSTICS:MPLABCommTool is null

394 1745177538495 GEN4_TO_CONTROLLER_LOG:GEN4_CONNECT_INT_LOG_AVR128DB48 Pre:GetFirmwareInfo
394 1745177538495 GEN4_TO_CONTROLLER_LOG:GEN4_CONNECT_INT_LOG_AVR128DB48 Payload
394 1745177538495 GEN4_TO_CONTROLLER_LOG:GEN4_CONNECT_INT_LOG_AVR128DB48 null
394 1745177538495 GEN4_TO_CONTROLLER_LOG:GEN4_CONNECT_INT_LOG_AVR128DB48 Payload End
394 1745177538502 GEN4_TO_CONTROLLER_LOG:GEN4_CONNECT_INT_LOG_AVR128DB48 Post:GetFirmwareInfo
394 1745177538502 GEN4_TO_CONTROLLER_LOG:GEN4_CONNECT_INT_LOG_AVR128DB48 Return Value
394 1745177538502 GEN4_TO_CONTROLLER_LOG:GEN4_CONNECT_INT_LOG_AVR128DB48 FirmwareInfo: Values:
394 1745177538502 GEN4_TO_CONTROLLER_LOG:GEN4_CONNECT_INT_LOG_AVR128DB48 FirmwareInfo: boot = false, bootVer = 01.00.00, apVer = 02.01.06, fpgaVer = ff.ff.ff, scriptVer = 00.06.71, macAddress = 0495683578451535052485156485252, devID = a1020e01, devID1 = 1, devSN0 = ffffffff, devSN1 = ffffffff, serialNumber = 021038102RYN005698, appCommitID = null, scriptCommitID = 74cdf38a4d, PCB_ID = 2
394 1745177538502 GEN4_TO_CONTROLLER_LOG:GEN4_CONNECT_INT_LOG_AVR128DB48 Return End

394 1745177538502 GEN4_TO_CONTROLLER_LOG:GEN4_CONNECT_INT_LOG_AVR128DB48 Pre:SetPowerInfo
394 1745177538502 GEN4_TO_CONTROLLER_LOG:GEN4_CONNECT_INT_LOG_AVR128DB48 Payload
394 1745177538502 GEN4_TO_CONTROLLER_LOG:GEN4_CONNECT_INT_LOG_AVR128DB48 PowerInfo: Values:
394 1745177538502 GEN4_TO_CONTROLLER_LOG:GEN4_CONNECT_INT_LOG_AVR128DB48 PowerInfo: shotDownSystem = false, isToolPower = false, voltage = 3.300000, useVppFirst = false, useLowVoltageProgramming = true, useMaintainActivePower = false
394 1745177538502 GEN4_TO_CONTROLLER_LOG:GEN4_CONNECT_INT_LOG_AVR128DB48 Payload End
394 1745177538503 XXXX 1745177538503, Thread 394: XXXX 1745177538503, Entering Thread 394: Commands::runScriptBasic with script contents. contents[0] = 0x39, ...  
394 1745177538504 XXXX 1745177538504, Thread 394: XXXX 1745177538504, Exiting Thread 394: Commands::runScriptBasic  
394 1745177538504 XXXX 1745177538504, Thread 394: XXXX 1745177538504, Entering Thread 394: Commands::runScriptBasic with script contents. contents[0] = 0x46, ...  
394 1745177538505 XXXX 1745177538504, Thread 394: XXXX 1745177538504, Exiting Thread 394: Commands::runScriptBasic  
394 1745177538505 XXXX 1745177538505, Thread 394: XXXX 1745177538505, Entering Thread 394: Commands::runScriptBasic with script contents. contents[0] = 0x44, ...  
394 1745177538506 XXXX 1745177538506, Thread 394: XXXX 1745177538506, Exiting Thread 394: Commands::runScriptBasic  
394 1745177538506 XXXX 1745177538506, Thread 394: XXXX 1745177538506, Entering Thread 394: Commands::runScriptBasic with script contents. contents[0] = 0xef, ...  
394 1745177538507 XXXX 1745177538507, Thread 394: XXXX 1745177538507, Exiting Thread 394: Commands::runScriptBasic  
394 1745177538507 XXXX 1745177538507, Thread 394: XXXX 1745177538507, Entering Thread 394: Commands::runScriptBasic with script contents. contents[0] = 0x40, ...  
394 1745177538508 XXXX 1745177538508, Thread 394: XXXX 1745177538508, Exiting Thread 394: Commands::runScriptBasic  
394 1745177538508 XXXX 1745177538508, Thread 394: XXXX 1745177538508, Entering Thread 394: Commands::runScriptBasic with script contents. contents[0] = 0x47, ...  
394 1745177538509 XXXX 1745177538509, Thread 394: XXXX 1745177538509, Exiting Thread 394: Commands::runScriptBasic  
394 1745177538509 GEN4_TO_CONTROLLER_LOG:GEN4_CONNECT_INT_LOG_AVR128DB48 Post:SetPowerInfo
394 1745177538509 GEN4_TO_CONTROLLER_LOG:GEN4_CONNECT_INT_LOG_AVR128DB48 Return Value
394 1745177538509 GEN4_TO_CONTROLLER_LOG:GEN4_CONNECT_INT_LOG_AVR128DB48 none
394 1745177538509 GEN4_TO_CONTROLLER_LOG:GEN4_CONNECT_INT_LOG_AVR128DB48 Return End
394 1745177538510 GEN4_CONNECT_DIAGNOSTICS:Removing plug and play observer com.microchip.mplab.mdbcore.RI4Tool.RI4ToolBase$RI4PlugNPlayObserver@4ba0742e
394 1745177538510 GEN4_CONNECT_DIAGNOSTICS:Begin PlugNPlayObservers list dump:
394 1745177538510 GEN4_CONNECT_DIAGNOSTICS:End PlugNPlayObservers list dump:
394 1745177538562 GEN4_CONNECT_DIAGNOSTICS:Calling RIDbgToolCom.Disconnect
394 1745177538562 GEN4_CONNECT_DIAGNOSTICS:Calling MPLABCommTool.Detach to remove tool from plug and play list
394 1745177538562 GEN4_CONNECT_DIAGNOSTICS:Calling RIDbgToolCom.DisconnectFromMPlabComm
394 1745177538562 GEN4_CONNECT_DIAGNOSTICS:Calling MPLABCommTool.Disconnect
408 1745177547848 GEN4_CONNECT_DIAGNOSTICS:MPLABCommTool is NOT null
408 1745177547848 GEN4_CONNECT_DIAGNOSTICS:AttachedToolPID = 9018, AttachedToolVID = 4d8
408 1745177547848 GEN4_CONNECT_DIAGNOSTICS:transport type = USB
408 1745177547848 GEN4_CONNECT_DIAGNOSTICS:AttachedToolPID = 9018, AttachedToolVID = 4d8
408 1745177547858 com.microchip.mplab.mdbcore.RealICETool.RIDbgToolCom
408 1745177547858 GEN4_CONNECT_DIAGNOSTICS:Before MPLABCommTool.Connect()
408 1745177547858 GEN4_CONNECT_DIAGNOSTICS:After MPLABCommTool.Connect()
408 1745177547858 GEN4_CONNECT_DIAGNOSTICS:MPLABCommTool.Connect() returned MPLABCOMM_NO_ERROR
408 1745177547858 GEN4_CONNECT_DIAGNOSTICS:Attaching to MPLABCommTool plugnplay
408 1745177547858 GEN4_CONNECT_DIAGNOSTICS:Adding new plug and play observer com.microchip.mplab.mdbcore.RI4Tool.RI4ToolBase$RI4PlugNPlayObserver@3cd2578d
408 1745177547858 GEN4_CONNECT_DIAGNOSTICS:Begin PlugNPlayObservers list dump:
408 1745177547858 GEN4_CONNECT_DIAGNOSTICS:com.microchip.mplab.mdbcore.RI4Tool.RI4ToolBase$RI4PlugNPlayObserver@3cd2578d
408 1745177547858 GEN4_CONNECT_DIAGNOSTICS:End PlugNPlayObservers list dump:
408 1745177547858 GEN4_CONNECT_DIAGNOSTICS:Registering for alternate PNP notifications. CommPnPCriteria.cPIDList = [9019, 901c, 2180], CommPnPCriteria.cSerialNumber = 021038102ryn005698

408 1745177547979 GEN4_TO_CONTROLLER_LOG:GEN4_INIT_INT_LOG_AVR128DB48 Pre:init
408 1745177547979 GEN4_TO_CONTROLLER_LOG:GEN4_INIT_INT_LOG_AVR128DB48 Payload
408 1745177547979 GEN4_TO_CONTROLLER_LOG:GEN4_INIT_INT_LOG_AVR128DB48 DeviceInfo: Values:
408 1745177547979 GEN4_TO_CONTROLLER_LOG:GEN4_INIT_INT_LOG_AVR128DB48 DeviceInfo: pcAddress = 7fffffffffffffff, Vpp = 5.00, useRowEraseIfVoltageIsLow = false, voltageBelowWhichUseRowErase = 0.00, deviceName = AVR128DB48, programmerType = AVR
408 1745177547979 GEN4_TO_CONTROLLER_LOG:GEN4_INIT_INT_LOG_AVR128DB48 DeviceInfo: MemInfo values:
408 1745177547979 GEN4_TO_CONTROLLER_LOG:GEN4_INIT_INT_LOG_AVR128DB48 DeviceInfo: mask = ffff, exists = true, startAddr = 00000000, endAddr = 0001ffff, rowSize = 0200, rowEraseSize = 0200, addrInc = 0001, widthProgram = 0001
408 1745177547979 GEN4_TO_CONTROLLER_LOG:GEN4_INIT_INT_LOG_AVR128DB48 DeviceInfo: mask = 00ff, exists = true, startAddr = 00821050, endAddr = 00831043, rowSize = 0001, rowEraseSize = 0000, addrInc = 0001, widthProgram = 0001
408 1745177547979 GEN4_TO_CONTROLLER_LOG:GEN4_INIT_INT_LOG_AVR128DB48 DeviceInfo: mask = 0000, exists = false, startAddr = 00000000, endAddr = 00000000, rowSize = 0000, rowEraseSize = 0000, addrInc = 0000, widthProgram = 0000
408 1745177547979 GEN4_TO_CONTROLLER_LOG:GEN4_INIT_INT_LOG_AVR128DB48 DeviceInfo: mask = 00ff, exists = true, startAddr = 00001400, endAddr = 000015ff, rowSize = 0001, rowEraseSize = 0000, addrInc = 0001, widthProgram = 0001
408 1745177547979 GEN4_TO_CONTROLLER_LOG:GEN4_INIT_INT_LOG_AVR128DB48 DeviceInfo: mask = 00ff, exists = true, startAddr = 00001080, endAddr = 0000109f, rowSize = 0020, rowEraseSize = 0000, addrInc = 0001, widthProgram = 0001
408 1745177547979 GEN4_TO_CONTROLLER_LOG:GEN4_INIT_INT_LOG_AVR128DB48 DeviceInfo: mask = 0000, exists = false, startAddr = 00000000, endAddr = 00000000, rowSize = 0000, rowEraseSize = 0200, addrInc = 0000, widthProgram = 0000
408 1745177547979 GEN4_TO_CONTROLLER_LOG:GEN4_INIT_INT_LOG_AVR128DB48 DeviceInfo: mask = 0000, exists = false, startAddr = 00000000, endAddr = 00000000, rowSize = 0000, rowEraseSize = 0000, addrInc = 0001, widthProgram = 0001
408 1745177547979 GEN4_TO_CONTROLLER_LOG:GEN4_INIT_INT_LOG_AVR128DB48 DeviceInfo: mask = 0000, exists = false, startAddr = 00000000, endAddr = 00000000, rowSize = 0000, rowEraseSize = 0000, addrInc = 0000, widthProgram = 0000
408 1745177547979 GEN4_TO_CONTROLLER_LOG:GEN4_INIT_INT_LOG_AVR128DB48 DeviceInfo: mask = 0000, exists = false, startAddr = 00000000, endAddr = 00000000, rowSize = 0000, rowEraseSize = 0000, addrInc = 0000, widthProgram = 0000
408 1745177547979 GEN4_TO_CONTROLLER_LOG:GEN4_INIT_INT_LOG_AVR128DB48 DeviceInfo: mask = 0000, exists = false, startAddr = 00000000, endAddr = 00000000, rowSize = 0000, rowEraseSize = 0000, addrInc = 0000, widthProgram = 0000
408 1745177547979 GEN4_TO_CONTROLLER_LOG:GEN4_INIT_INT_LOG_AVR128DB48 DeviceInfo: mask = 0000, exists = false, startAddr = 00000000, endAddr = 00000000, rowSize = 0000, rowEraseSize = 0000, addrInc = 0000, widthProgram = 0000
408 1745177547979 GEN4_TO_CONTROLLER_LOG:GEN4_INIT_INT_LOG_AVR128DB48 DeviceInfo: mask = 0000, exists = false, startAddr = 00000000, endAddr = 00000000, rowSize = 0000, rowEraseSize = 0000, addrInc = 0001, widthProgram = 0001
408 1745177547979 GEN4_TO_CONTROLLER_LOG:GEN4_INIT_INT_LOG_AVR128DB48 DeviceInfo: mask = 0000, exists = false, startAddr = 00000000, endAddr = 00000000, rowSize = 0000, rowEraseSize = 0000, addrInc = 0000, widthProgram = 0000
408 1745177547979 GEN4_TO_CONTROLLER_LOG:GEN4_INIT_INT_LOG_AVR128DB48 DeviceInfo: mask = 0000, exists = false, startAddr = 00000000, endAddr = 00000000, rowSize = 0000, rowEraseSize = 0000, addrInc = 0000, widthProgram = 0000
408 1745177547979 GEN4_TO_CONTROLLER_LOG:GEN4_INIT_INT_LOG_AVR128DB48 DeviceInfo: mask = 0000, exists = false, startAddr = 00000000, endAddr = 00000000, rowSize = 0000, rowEraseSize = 0000, addrInc = 0000, widthProgram = 0000
408 1745177547979 GEN4_TO_CONTROLLER_LOG:GEN4_INIT_INT_LOG_AVR128DB48 DeviceInfo: mask = 0000, exists = false, startAddr = 00000000, endAddr = 00000000, rowSize = 0000, rowEraseSize = 0000, addrInc = 0000, widthProgram = 0000
408 1745177547979 GEN4_TO_CONTROLLER_LOG:GEN4_INIT_INT_LOG_AVR128DB48 DeviceInfo: mask = 7fffffff, exists = true, startAddr = 00001100, endAddr = 0000117f, rowSize = 0001, rowEraseSize = 0000, addrInc = 0001, widthProgram = 0001
408 1745177547979 GEN4_TO_CONTROLLER_LOG:GEN4_INIT_INT_LOG_AVR128DB48 DeviceInfo: mask = 0000, exists = false, startAddr = 00000000, endAddr = 00000000, rowSize = 0000, rowEraseSize = 0000, addrInc = 0000, widthProgram = 0000
408 1745177547979 GEN4_TO_CONTROLLER_LOG:GEN4_INIT_INT_LOG_AVR128DB48 DeviceInfo: mask = 0000, exists = false, startAddr = 00000000, endAddr = 00000000, rowSize = 0000, rowEraseSize = 0000, addrInc = 0000, widthProgram = 0000
408 1745177547979 GEN4_TO_CONTROLLER_LOG:GEN4_INIT_INT_LOG_AVR128DB48 DeviceInfo: mask = 0000, exists = false, startAddr = 00000000, endAddr = 00000000, rowSize = 0000, rowEraseSize = 0000, addrInc = 0000, widthProgram = 0000
408 1745177547979 GEN4_TO_CONTROLLER_LOG:GEN4_INIT_INT_LOG_AVR128DB48 DeviceInfo: mask = 0000, exists = false, startAddr = 00000000, endAddr = 00000000, rowSize = 0000, rowEraseSize = 0000, addrInc = 0000, widthProgram = 0000
408 1745177547980 GEN4_TO_CONTROLLER_LOG:GEN4_INIT_INT_LOG_AVR128DB48 DeviceInfo: mask = 0000, exists = false, startAddr = 00000000, endAddr = 00000000, rowSize = 0000, rowEraseSize = 0000, addrInc = 0000, widthProgram = 0000
408 1745177547980 GEN4_TO_CONTROLLER_LOG:GEN4_INIT_INT_LOG_AVR128DB48 DeviceInfo: mask = 0000, exists = false, startAddr = 00000000, endAddr = 00000000, rowSize = 0000, rowEraseSize = 0000, addrInc = 0000, widthProgram = 0000
408 1745177547980 GEN4_TO_CONTROLLER_LOG:GEN4_INIT_INT_LOG_AVR128DB48 CfgRequiredBitsMask Values:
408 1745177547980 GEN4_TO_CONTROLLER_LOG:GEN4_INIT_INT_LOG_AVR128DB48 Address = 00001100, Mask = 00000000
408 1745177547980 GEN4_TO_CONTROLLER_LOG:GEN4_INIT_INT_LOG_AVR128DB48 Address = 00001101, Mask = 00000000
408 1745177547980 GEN4_TO_CONTROLLER_LOG:GEN4_INIT_INT_LOG_AVR128DB48 Address = 00001102, Mask = 00000000
408 1745177547980 GEN4_TO_CONTROLLER_LOG:GEN4_INIT_INT_LOG_AVR128DB48 Address = 00001104, Mask = 0000ffff
408 1745177547980 GEN4_TO_CONTROLLER_LOG:GEN4_INIT_INT_LOG_AVR128DB48 Address = 00001106, Mask = 0000ffff
408 1745177547980 GEN4_TO_CONTROLLER_LOG:GEN4_INIT_INT_LOG_AVR128DB48 Address = 00001110, Mask = 00000000
408 1745177547980 GEN4_TO_CONTROLLER_LOG:GEN4_INIT_INT_LOG_AVR128DB48 Address = 00001111, Mask = 00000000
408 1745177547980 GEN4_TO_CONTROLLER_LOG:GEN4_INIT_INT_LOG_AVR128DB48 Address = 00001112, Mask = 00000000
408 1745177547980 GEN4_TO_CONTROLLER_LOG:GEN4_INIT_INT_LOG_AVR128DB48 Address = 00001113, Mask = 00000000
408 1745177547980 GEN4_TO_CONTROLLER_LOG:GEN4_INIT_INT_LOG_AVR128DB48 Address = 00001114, Mask = 00000000
408 1745177547980 GEN4_TO_CONTROLLER_LOG:GEN4_INIT_INT_LOG_AVR128DB48 Address = 00001115, Mask = 00000000
408 1745177547980 GEN4_TO_CONTROLLER_LOG:GEN4_INIT_INT_LOG_AVR128DB48 Address = 00001116, Mask = 00000000
408 1745177547980 GEN4_TO_CONTROLLER_LOG:GEN4_INIT_INT_LOG_AVR128DB48 Address = 00001117, Mask = 00000000
408 1745177547980 GEN4_TO_CONTROLLER_LOG:GEN4_INIT_INT_LOG_AVR128DB48 Address = 00001118, Mask = 00000000
408 1745177547980 GEN4_TO_CONTROLLER_LOG:GEN4_INIT_INT_LOG_AVR128DB48 Address = 00001119, Mask = 00000000
408 1745177547980 GEN4_TO_CONTROLLER_LOG:GEN4_INIT_INT_LOG_AVR128DB48 Address = 0000111a, Mask = 00000000
408 1745177547980 GEN4_TO_CONTROLLER_LOG:GEN4_INIT_INT_LOG_AVR128DB48 Address = 0000111b, Mask = 00000000
408 1745177547980 GEN4_TO_CONTROLLER_LOG:GEN4_INIT_INT_LOG_AVR128DB48 Address = 0000111c, Mask = 00000000
408 1745177547980 GEN4_TO_CONTROLLER_LOG:GEN4_INIT_INT_LOG_AVR128DB48 Address = 0000111d, Mask = 00000000
408 1745177547980 GEN4_TO_CONTROLLER_LOG:GEN4_INIT_INT_LOG_AVR128DB48 Address = 0000111e, Mask = 00000000
408 1745177547980 GEN4_TO_CONTROLLER_LOG:GEN4_INIT_INT_LOG_AVR128DB48 Address = 0000111f, Mask = 00000000
408 1745177547980 GEN4_TO_CONTROLLER_LOG:GEN4_INIT_INT_LOG_AVR128DB48 Address = 00821050, Mask = 000000ff
408 1745177547980 GEN4_TO_CONTROLLER_LOG:GEN4_INIT_INT_LOG_AVR128DB48 Address = 00821051, Mask = 000000ff
408 1745177547980 GEN4_TO_CONTROLLER_LOG:GEN4_INIT_INT_LOG_AVR128DB48 Address = 00821052, Mask = 00000007
408 1745177547980 GEN4_TO_CONTROLLER_LOG:GEN4_INIT_INT_LOG_AVR128DB48 Address = 00821055, Mask = 000000ed
408 1745177547980 GEN4_TO_CONTROLLER_LOG:GEN4_INIT_INT_LOG_AVR128DB48 Address = 00821056, Mask = 0000001f
408 1745177547980 GEN4_TO_CONTROLLER_LOG:GEN4_INIT_INT_LOG_AVR128DB48 Address = 00821057, Mask = 000000ff
408 1745177547980 GEN4_TO_CONTROLLER_LOG:GEN4_INIT_INT_LOG_AVR128DB48 Address = 00821058, Mask = 000000ff
408 1745177547980 GEN4_TO_CONTROLLER_LOG:GEN4_INIT_INT_LOG_AVR128DB48 Address = 00831040, Mask = ffffffff
408 1745177547980 GEN4_TO_CONTROLLER_LOG:GEN4_INIT_INT_LOG_AVR128DB48 BasicInfo: Values:
408 1745177547980 GEN4_TO_CONTROLLER_LOG:GEN4_INIT_INT_LOG_AVR128DB48 Payload End
408 1745177547981 GEN4_TO_CONTROLLER_LOG:GEN4_INIT_INT_LOG_AVR128DB48 Post:init
408 1745177547981 GEN4_TO_CONTROLLER_LOG:GEN4_INIT_INT_LOG_AVR128DB48 Return Value
408 1745177547981 GEN4_TO_CONTROLLER_LOG:GEN4_INIT_INT_LOG_AVR128DB48 none
408 1745177547981 GEN4_TO_CONTROLLER_LOG:GEN4_INIT_INT_LOG_AVR128DB48 Return End

408 1745177547981 GEN4_TO_CONTROLLER_LOG:GEN4_INIT_INT_LOG_AVR128DB48 Pre:GetInterfaceProvider
408 1745177547981 GEN4_TO_CONTROLLER_LOG:GEN4_INIT_INT_LOG_AVR128DB48 Payload
408 1745177547981 GEN4_TO_CONTROLLER_LOG:GEN4_INIT_INT_LOG_AVR128DB48 RI4DebugInterface
408 1745177547981 GEN4_TO_CONTROLLER_LOG:GEN4_INIT_INT_LOG_AVR128DB48 Payload End
408 1745177547981 GEN4_TO_CONTROLLER_LOG:GEN4_INIT_INT_LOG_AVR128DB48 Post:GetInterfaceProvider
408 1745177547981 GEN4_TO_CONTROLLER_LOG:GEN4_INIT_INT_LOG_AVR128DB48 Return Value
408 1745177547981 GEN4_TO_CONTROLLER_LOG:GEN4_INIT_INT_LOG_AVR128DB48 com.microchip.mplab.libs.RI4ToolsController.implementations.RI4DebugInterfaceImpl@596180ca
408 1745177547981 GEN4_TO_CONTROLLER_LOG:GEN4_INIT_INT_LOG_AVR128DB48 Return End

408 1745177547981 GEN4_TO_CONTROLLER_LOG:GEN4_INIT_INT_LOG_AVR128DB48 Pre:GetInterfaceProvider
408 1745177547981 GEN4_TO_CONTROLLER_LOG:GEN4_INIT_INT_LOG_AVR128DB48 Payload
408 1745177547981 GEN4_TO_CONTROLLER_LOG:GEN4_INIT_INT_LOG_AVR128DB48 RI4ProgramInterface
408 1745177547981 GEN4_TO_CONTROLLER_LOG:GEN4_INIT_INT_LOG_AVR128DB48 Payload End
408 1745177547981 GEN4_TO_CONTROLLER_LOG:GEN4_INIT_INT_LOG_AVR128DB48 Post:GetInterfaceProvider
408 1745177547981 GEN4_TO_CONTROLLER_LOG:GEN4_INIT_INT_LOG_AVR128DB48 Return Value
408 1745177547981 GEN4_TO_CONTROLLER_LOG:GEN4_INIT_INT_LOG_AVR128DB48 com.microchip.mplab.libs.RI4ToolsController.implementations.RI4ProgramInterfaceImpl@16dcdc9f
408 1745177547981 GEN4_TO_CONTROLLER_LOG:GEN4_INIT_INT_LOG_AVR128DB48 Return End

408 1745177547981 GEN4_TO_CONTROLLER_LOG:GEN4_INIT_INT_LOG_AVR128DB48 Pre:GetInterfaceProvider
408 1745177547981 GEN4_TO_CONTROLLER_LOG:GEN4_INIT_INT_LOG_AVR128DB48 Payload
408 1745177547981 GEN4_TO_CONTROLLER_LOG:GEN4_INIT_INT_LOG_AVR128DB48 RI4ConnectInterface
408 1745177547981 GEN4_TO_CONTROLLER_LOG:GEN4_INIT_INT_LOG_AVR128DB48 Payload End
408 1745177547982 GEN4_TO_CONTROLLER_LOG:GEN4_INIT_INT_LOG_AVR128DB48 Post:GetInterfaceProvider
408 1745177547982 GEN4_TO_CONTROLLER_LOG:GEN4_INIT_INT_LOG_AVR128DB48 Return Value
408 1745177547982 GEN4_TO_CONTROLLER_LOG:GEN4_INIT_INT_LOG_AVR128DB48 com.microchip.mplab.libs.PK4ToolsController.PK4ConnectInterfaceImpl@389c8ff6
408 1745177547982 GEN4_TO_CONTROLLER_LOG:GEN4_INIT_INT_LOG_AVR128DB48 Return End
408 1745177547982 GEN4_CONNECT_DIAGNOSTICS:acceptablePIDs = [9018, 9019, 901c]
408 1745177547982 GEN4_CONNECT_DIAGNOSTICS:otherPIDs = [2180]
408 1745177547982 GEN4_CONNECT_DIAGNOSTICS:Setting selected tool type to pk4
408 1745177547982 GEN4_CONNECT_DIAGNOSTICS:otherPIDs = [2180]
408 1745177547982 GEN4_CONNECT_DIAGNOSTICS:acceptablePIDs = [9018, 9019, 901c]

408 1745177547982 GEN4_TO_CONTROLLER_LOG:GEN4_INIT_INT_LOG_AVR128DB48 Pre:GetInterfaceProvider
408 1745177547982 GEN4_TO_CONTROLLER_LOG:GEN4_INIT_INT_LOG_AVR128DB48 Payload
408 1745177547982 GEN4_TO_CONTROLLER_LOG:GEN4_INIT_INT_LOG_AVR128DB48 RI4ControllerDiagnosticsInterface
408 1745177547982 GEN4_TO_CONTROLLER_LOG:GEN4_INIT_INT_LOG_AVR128DB48 Payload End
408 1745177547982 GEN4_TO_CONTROLLER_LOG:GEN4_INIT_INT_LOG_AVR128DB48 Post:GetInterfaceProvider
408 1745177547982 GEN4_TO_CONTROLLER_LOG:GEN4_INIT_INT_LOG_AVR128DB48 Return Value
408 1745177547982 GEN4_TO_CONTROLLER_LOG:GEN4_INIT_INT_LOG_AVR128DB48 com.microchip.mplab.libs.RI4ToolsController.implementations.RI4ControllerDiagnosticsInterfaceImpl@1358eb89
408 1745177547982 GEN4_TO_CONTROLLER_LOG:GEN4_INIT_INT_LOG_AVR128DB48 Return End

408 1745177547982 GEN4_TO_CONTROLLER_LOG:GEN4_INIT_INT_LOG_AVR128DB48 Pre:GetInterfaceProvider
408 1745177547982 GEN4_TO_CONTROLLER_LOG:GEN4_INIT_INT_LOG_AVR128DB48 Payload
408 1745177547982 GEN4_TO_CONTROLLER_LOG:GEN4_INIT_INT_LOG_AVR128DB48 ProgrammerToGo
408 1745177547982 GEN4_TO_CONTROLLER_LOG:GEN4_INIT_INT_LOG_AVR128DB48 Payload End
408 1745177547982 GEN4_TO_CONTROLLER_LOG:GEN4_INIT_INT_LOG_AVR128DB48 Post:GetInterfaceProvider
408 1745177547982 GEN4_TO_CONTROLLER_LOG:GEN4_INIT_INT_LOG_AVR128DB48 Return Value
408 1745177547982 GEN4_TO_CONTROLLER_LOG:GEN4_INIT_INT_LOG_AVR128DB48 com.microchip.mplab.libs.RI4ToolsController.implementations.ProgrammerToGoImpl@46ea5ef8
408 1745177547982 GEN4_TO_CONTROLLER_LOG:GEN4_INIT_INT_LOG_AVR128DB48 Return End

408 1745177547982 GEN4_TO_CONTROLLER_LOG:GEN4_INIT_INT_LOG_AVR128DB48 Pre:GetInterfaceProvider
408 1745177547982 GEN4_TO_CONTROLLER_LOG:GEN4_INIT_INT_LOG_AVR128DB48 Payload
408 1745177547982 GEN4_TO_CONTROLLER_LOG:GEN4_INIT_INT_LOG_AVR128DB48 Status
408 1745177547982 GEN4_TO_CONTROLLER_LOG:GEN4_INIT_INT_LOG_AVR128DB48 Payload End
408 1745177547982 GEN4_TO_CONTROLLER_LOG:GEN4_INIT_INT_LOG_AVR128DB48 Post:GetInterfaceProvider
408 1745177547982 GEN4_TO_CONTROLLER_LOG:GEN4_INIT_INT_LOG_AVR128DB48 Return Value
408 1745177547982 GEN4_TO_CONTROLLER_LOG:GEN4_INIT_INT_LOG_AVR128DB48 null
408 1745177547982 GEN4_TO_CONTROLLER_LOG:GEN4_INIT_INT_LOG_AVR128DB48 Return End
408 1745177547989 GEN4_CONNECT_DIAGNOSTICS:ENTERING: com.microchip.mplab.mdbcore.RI4Tool.ConnectionHandler.CheckForFWUpdates()
408 1745177547989 GEN4_CONNECT_DIAGNOSTICS:Created FirmwareUpdateHandler com.microchip.mplab.mdbcore.pk4hybrid.pk4hybridFirmwareUpdateHandler@36225a9e
408 1745177547989 GEN4_CONNECT_DIAGNOSTICS:ENTERING: com.microchip.mplab.mdbcore.pk4hybrid.pk4hybridFirmwareUpdateHandler.UpdateFirmware(FirmwareInfo, UpdateMessage)
408 1745177547989 GEN4_CONNECT_DIAGNOSTICS:areWeInBoot returned false
408 1745177547989 GEN4_CONNECT_DIAGNOSTICS:inBoot = false
408 1745177547989 GEN4_CONNECT_DIAGNOSTICS:uMode = checkingVersions
408 1745177547989 GEN4_CONNECT_DIAGNOSTICS:selectedTool = pk4
408 1745177547989 GEN4_CONNECT_DIAGNOSTICS:current toolType = pk4
408 1745177547989 GEN4_CONNECT_DIAGNOSTICS:current tool mode = pk4
408 1745177547989 GEN4_CONNECT_DIAGNOSTICS:ENTERING: com.microchip.mplab.mdbcore.pk4hybrid.pk4hybridFirmwareUpdateHandler.GetUpdateInfo()
408 1745177547990 GEN4_CONNECT_DIAGNOSTICS:Parsing file  for firmware updates
408 1745177547990 GEN4_CONNECT_DIAGNOSTICS:ENTERING: com.microchip.mplab.mdbcore.pk4hybrid.pk4hybridFirmwareUpdateHandler.ParseSelectedVersionsFromJamFile()
408 1745177547990 GEN4_CONNECT_DIAGNOSTICS:Jame file line = snap_boot.hex,010000
408 1745177547990 GEN4_CONNECT_DIAGNOSTICS:Jame file line = scripts.xml,000671
408 1745177547990 GEN4_CONNECT_DIAGNOSTICS:Jame file line = snap_app1 020106, 0040C000
408 1745177547990 GEN4_CONNECT_DIAGNOSTICS:Jame file line = snap_app2 1.11.20, 00500000
408 1745177547990 GEN4_CONNECT_DIAGNOSTICS:Jame file line = snap_app3 000000, FFFFFFFF
408 1745177547990 GEN4_CONNECT_DIAGNOSTICS:Jame file line = snap_app4 000000, FFFFFFFF
408 1745177547990 GEN4_CONNECT_DIAGNOSTICS:Jame file line = snap_app5 000000, FFFFFFFF
408 1745177547990 GEN4_CONNECT_DIAGNOSTICS:Jame file line = snap_app6 000000, FFFFFFFF
408 1745177547990 GEN4_CONNECT_DIAGNOSTICS:Jame file line = snap_app7 000000, FFFFFFFF
408 1745177547990 GEN4_CONNECT_DIAGNOSTICS:Jame file line = snap_app8 000000, FFFFFFFF
408 1745177547990 GEN4_CONNECT_DIAGNOSTICS:EXITING: com.microchip.mplab.mdbcore.pk4hybrid.pk4hybridFirmwareUpdateHandler.ri4ParseSelectedVersionsFromJamFile()
408 1745177547990 GEN4_CONNECT_DIAGNOSTICS:EXITING: com.microchip.mplab.mdbcore.pk4hybrid.pk4hybridFirmwareUpdateHandler.GetUpdateInfo()
408 1745177547990 GEN4_CONNECT_DIAGNOSTICS:current toolType = pk4

408 1745177547990 GEN4_TO_CONTROLLER_LOG:GEN4_CONNECT_INT_LOG_AVR128DB48 Pre:EstablishCommunincations
408 1745177547990 GEN4_TO_CONTROLLER_LOG:GEN4_CONNECT_INT_LOG_AVR128DB48 Payload
408 1745177547990 GEN4_TO_CONTROLLER_LOG:GEN4_CONNECT_INT_LOG_AVR128DB48 com.microchip.mplab.mdbcore.PK4Tool.PK4Com@6deb7685
408 1745177547990 GEN4_TO_CONTROLLER_LOG:GEN4_CONNECT_INT_LOG_AVR128DB48 Payload End
408 1745177547990 GEN4_TO_CONTROLLER_LOG:GEN4_CONNECT_INT_LOG_AVR128DB48 Post:EstablishCommunincations
408 1745177547990 GEN4_TO_CONTROLLER_LOG:GEN4_CONNECT_INT_LOG_AVR128DB48 Return Value
408 1745177547990 GEN4_TO_CONTROLLER_LOG:GEN4_CONNECT_INT_LOG_AVR128DB48 true
408 1745177547990 GEN4_TO_CONTROLLER_LOG:GEN4_CONNECT_INT_LOG_AVR128DB48 Return End

408 1745177547990 GEN4_TO_CONTROLLER_LOG:GEN4_CONNECT_INT_LOG_AVR128DB48 Pre:GetFirmwareInfo
408 1745177547990 GEN4_TO_CONTROLLER_LOG:GEN4_CONNECT_INT_LOG_AVR128DB48 Payload
408 1745177547990 GEN4_TO_CONTROLLER_LOG:GEN4_CONNECT_INT_LOG_AVR128DB48 null
408 1745177547990 GEN4_TO_CONTROLLER_LOG:GEN4_CONNECT_INT_LOG_AVR128DB48 Payload End
408 1745177547998 GEN4_TO_CONTROLLER_LOG:GEN4_CONNECT_INT_LOG_AVR128DB48 Post:GetFirmwareInfo
408 1745177547998 GEN4_TO_CONTROLLER_LOG:GEN4_CONNECT_INT_LOG_AVR128DB48 Return Value
408 1745177547998 GEN4_TO_CONTROLLER_LOG:GEN4_CONNECT_INT_LOG_AVR128DB48 FirmwareInfo: Values:
408 1745177547998 GEN4_TO_CONTROLLER_LOG:GEN4_CONNECT_INT_LOG_AVR128DB48 FirmwareInfo: boot = false, bootVer = 01.00.00, apVer = 02.01.06, fpgaVer = ff.ff.ff, scriptVer = 00.06.71, macAddress = 0495683578451535052485156485252, devID = a1020e01, devID1 = 1, devSN0 = ffffffff, devSN1 = ffffffff, serialNumber = 021038102RYN005698, appCommitID = null, scriptCommitID = 74cdf38a4d, PCB_ID = 2
408 1745177547998 GEN4_TO_CONTROLLER_LOG:GEN4_CONNECT_INT_LOG_AVR128DB48 Return End
408 1745177548007 GEN4_CONNECT_DIAGNOSTICS:appNeedsUpdate returned false
408 1745177548007 GEN4_CONNECT_DIAGNOSTICS:EXITING: com.microchip.mplab.mdbcore.RI4Tool.ConnectionHandler.CheckForFWUpdates()

408 1745177548007 GEN4_TO_CONTROLLER_LOG:GEN4_CONNECT_INT_LOG_AVR128DB48 Pre:EstablishCommunincations
408 1745177548007 GEN4_TO_CONTROLLER_LOG:GEN4_CONNECT_INT_LOG_AVR128DB48 Payload
408 1745177548007 GEN4_TO_CONTROLLER_LOG:GEN4_CONNECT_INT_LOG_AVR128DB48 com.microchip.mplab.mdbcore.PK4Tool.PK4Com@6deb7685
408 1745177548007 GEN4_TO_CONTROLLER_LOG:GEN4_CONNECT_INT_LOG_AVR128DB48 Payload End
408 1745177548008 GEN4_TO_CONTROLLER_LOG:GEN4_CONNECT_INT_LOG_AVR128DB48 Post:EstablishCommunincations
408 1745177548008 GEN4_TO_CONTROLLER_LOG:GEN4_CONNECT_INT_LOG_AVR128DB48 Return Value
408 1745177548008 GEN4_TO_CONTROLLER_LOG:GEN4_CONNECT_INT_LOG_AVR128DB48 true
408 1745177548008 GEN4_TO_CONTROLLER_LOG:GEN4_CONNECT_INT_LOG_AVR128DB48 Return End

408 1745177548008 GEN4_TO_CONTROLLER_LOG:GEN4_CONNECT_INT_LOG_AVR128DB48 Pre:GetFirmwareInfo
408 1745177548008 GEN4_TO_CONTROLLER_LOG:GEN4_CONNECT_INT_LOG_AVR128DB48 Payload
408 1745177548008 GEN4_TO_CONTROLLER_LOG:GEN4_CONNECT_INT_LOG_AVR128DB48 null
408 1745177548008 GEN4_TO_CONTROLLER_LOG:GEN4_CONNECT_INT_LOG_AVR128DB48 Payload End
408 1745177548016 GEN4_TO_CONTROLLER_LOG:GEN4_CONNECT_INT_LOG_AVR128DB48 Post:GetFirmwareInfo
408 1745177548016 GEN4_TO_CONTROLLER_LOG:GEN4_CONNECT_INT_LOG_AVR128DB48 Return Value
408 1745177548016 GEN4_TO_CONTROLLER_LOG:GEN4_CONNECT_INT_LOG_AVR128DB48 FirmwareInfo: Values:
408 1745177548016 GEN4_TO_CONTROLLER_LOG:GEN4_CONNECT_INT_LOG_AVR128DB48 FirmwareInfo: boot = false, bootVer = 01.00.00, apVer = 02.01.06, fpgaVer = ff.ff.ff, scriptVer = 00.06.71, macAddress = 0495683578451535052485156485252, devID = a1020e01, devID1 = 1, devSN0 = ffffffff, devSN1 = ffffffff, serialNumber = 021038102RYN005698, appCommitID = null, scriptCommitID = 74cdf38a4d, PCB_ID = 2
408 1745177548016 GEN4_TO_CONTROLLER_LOG:GEN4_CONNECT_INT_LOG_AVR128DB48 Return End

408 1745177548016 GEN4_TO_CONTROLLER_LOG:GEN4_CONNECT_INT_LOG_AVR128DB48 Pre:GetFirmwareInfo
408 1745177548016 GEN4_TO_CONTROLLER_LOG:GEN4_CONNECT_INT_LOG_AVR128DB48 Payload
408 1745177548016 GEN4_TO_CONTROLLER_LOG:GEN4_CONNECT_INT_LOG_AVR128DB48 null
408 1745177548016 GEN4_TO_CONTROLLER_LOG:GEN4_CONNECT_INT_LOG_AVR128DB48 Payload End
408 1745177548024 GEN4_TO_CONTROLLER_LOG:GEN4_CONNECT_INT_LOG_AVR128DB48 Post:GetFirmwareInfo
408 1745177548024 GEN4_TO_CONTROLLER_LOG:GEN4_CONNECT_INT_LOG_AVR128DB48 Return Value
408 1745177548024 GEN4_TO_CONTROLLER_LOG:GEN4_CONNECT_INT_LOG_AVR128DB48 FirmwareInfo: Values:
408 1745177548024 GEN4_TO_CONTROLLER_LOG:GEN4_CONNECT_INT_LOG_AVR128DB48 FirmwareInfo: boot = false, bootVer = 01.00.00, apVer = 02.01.06, fpgaVer = ff.ff.ff, scriptVer = 00.06.71, macAddress = 0495683578451535052485156485252, devID = a1020e01, devID1 = 1, devSN0 = ffffffff, devSN1 = ffffffff, serialNumber = 021038102RYN005698, appCommitID = null, scriptCommitID = 74cdf38a4d, PCB_ID = 2
408 1745177548024 GEN4_TO_CONTROLLER_LOG:GEN4_CONNECT_INT_LOG_AVR128DB48 Return End
408 1745177548024 GEN4_CONNECT_DIAGNOSTICS:ENTERING: com.microchip.mplab.mdbcore.RI4Tool.ConnectionHandler.CheckForFWUpdates()
408 1745177548024 GEN4_CONNECT_DIAGNOSTICS:Created FirmwareUpdateHandler com.microchip.mplab.mdbcore.pk4hybrid.pk4hybridFirmwareUpdateHandler@36225a9e
408 1745177548024 GEN4_CONNECT_DIAGNOSTICS:ENTERING: com.microchip.mplab.mdbcore.pk4hybrid.pk4hybridFirmwareUpdateHandler.UpdateFirmware(FirmwareInfo, UpdateMessage)
408 1745177548024 GEN4_CONNECT_DIAGNOSTICS:areWeInBoot returned false
408 1745177548024 GEN4_CONNECT_DIAGNOSTICS:inBoot = false
408 1745177548024 GEN4_CONNECT_DIAGNOSTICS:uMode = done
408 1745177548024 GEN4_CONNECT_DIAGNOSTICS:selectedTool = pk4
408 1745177548024 GEN4_CONNECT_DIAGNOSTICS:current toolType = pk4
408 1745177548024 GEN4_CONNECT_DIAGNOSTICS:current tool mode = pk4
408 1745177548025 GEN4_CONNECT_DIAGNOSTICS:ENTERING: com.microchip.mplab.mdbcore.pk4hybrid.pk4hybridFirmwareUpdateHandler.updatePk4HybridFirmware()
408 1745177548025 GEN4_CONNECT_DIAGNOSTICS:Don't upgrade fimware = false
408 1745177548025 GEN4_CONNECT_DIAGNOSTICS:ENTERING: com.microchip.mplab.mdbcore.pk4hybrid.pk4hybridFirmwareUpdateHandler.updatePk4HybridFirmware()
408 1745177548025 GEN4_CONNECT_DIAGNOSTICS:EXITING: com.microchip.mplab.mdbcore.pk4hybrid.pk4hybridFirmwareUpdateHandler.UpdateFirmware(FirmwareInfo, UpdateMessage)
408 1745177548025 GEN4_CONNECT_DIAGNOSTICS:EXITING: com.microchip.mplab.mdbcore.RI4Tool.ConnectionHandler.CheckForFWUpdates()

408 1745177548025 GEN4_TO_CONTROLLER_LOG:GEN4_CONNECT_INT_LOG_AVR128DB48 Pre:SetPowerInfo
408 1745177548025 GEN4_TO_CONTROLLER_LOG:GEN4_CONNECT_INT_LOG_AVR128DB48 Payload
408 1745177548025 GEN4_TO_CONTROLLER_LOG:GEN4_CONNECT_INT_LOG_AVR128DB48 PowerInfo: Values:
408 1745177548025 GEN4_TO_CONTROLLER_LOG:GEN4_CONNECT_INT_LOG_AVR128DB48 PowerInfo: shotDownSystem = false, isToolPower = false, voltage = 3.300000, useVppFirst = false, useLowVoltageProgramming = true, useMaintainActivePower = false
408 1745177548025 GEN4_TO_CONTROLLER_LOG:GEN4_CONNECT_INT_LOG_AVR128DB48 Payload End
408 1745177548025 XXXX 1745177548025, Thread 408: XXXX 1745177548025, Entering Thread 408: Commands::runScriptBasic with script contents. contents[0] = 0x39, ...  
408 1745177548026 XXXX 1745177548026, Thread 408: XXXX 1745177548026, Exiting Thread 408: Commands::runScriptBasic  
408 1745177548026 XXXX 1745177548026, Thread 408: XXXX 1745177548026, Entering Thread 408: Commands::runScriptBasic with script contents. contents[0] = 0x46, ...  
408 1745177548027 XXXX 1745177548027, Thread 408: XXXX 1745177548027, Exiting Thread 408: Commands::runScriptBasic  
408 1745177548027 XXXX 1745177548027, Thread 408: XXXX 1745177548027, Entering Thread 408: Commands::runScriptBasic with script contents. contents[0] = 0x44, ...  
408 1745177548028 XXXX 1745177548028, Thread 408: XXXX 1745177548028, Exiting Thread 408: Commands::runScriptBasic  
408 1745177548028 XXXX 1745177548028, Thread 408: XXXX 1745177548028, Entering Thread 408: Commands::runScriptBasic with script contents. contents[0] = 0xef, ...  
408 1745177548029 XXXX 1745177548029, Thread 408: XXXX 1745177548029, Exiting Thread 408: Commands::runScriptBasic  
408 1745177548029 XXXX 1745177548029, Thread 408: XXXX 1745177548029, Entering Thread 408: Commands::runScriptBasic with script contents. contents[0] = 0x40, ...  
408 1745177548030 XXXX 1745177548030, Thread 408: XXXX 1745177548030, Exiting Thread 408: Commands::runScriptBasic  
408 1745177548030 XXXX 1745177548030, Thread 408: XXXX 1745177548030, Entering Thread 408: Commands::runScriptBasic with script contents. contents[0] = 0x47, ...  
408 1745177548031 XXXX 1745177548031, Thread 408: XXXX 1745177548031, Exiting Thread 408: Commands::runScriptBasic  
408 1745177548031 GEN4_TO_CONTROLLER_LOG:GEN4_CONNECT_INT_LOG_AVR128DB48 Post:SetPowerInfo
408 1745177548031 GEN4_TO_CONTROLLER_LOG:GEN4_CONNECT_INT_LOG_AVR128DB48 Return Value
408 1745177548031 GEN4_TO_CONTROLLER_LOG:GEN4_CONNECT_INT_LOG_AVR128DB48 none
408 1745177548031 GEN4_TO_CONTROLLER_LOG:GEN4_CONNECT_INT_LOG_AVR128DB48 Return End

408 1745177548031 GEN4_TO_CONTROLLER_LOG:GEN4_CONNECT_INT_LOG_AVR128DB48 Pre:GetVoltageInfo
408 1745177548031 GEN4_TO_CONTROLLER_LOG:GEN4_CONNECT_INT_LOG_AVR128DB48 Payload
408 1745177548031 GEN4_TO_CONTROLLER_LOG:GEN4_CONNECT_INT_LOG_AVR128DB48 null
408 1745177548031 GEN4_TO_CONTROLLER_LOG:GEN4_CONNECT_INT_LOG_AVR128DB48 Payload End
408 1745177548032 XXXX 1745177548032, Thread 408: XXXX 1745177548032, Entering Thread 408: Commands::runScriptBasic with script contents. contents[0] = 0x47, ...  
408 1745177548033 XXXX 1745177548033, Thread 408: XXXX 1745177548033, Exiting Thread 408: Commands::runScriptBasic  
408 1745177548033 GEN4_TO_CONTROLLER_LOG:GEN4_CONNECT_INT_LOG_AVR128DB48 Post:GetVoltageInfo
408 1745177548033 GEN4_TO_CONTROLLER_LOG:GEN4_CONNECT_INT_LOG_AVR128DB48 Return Value
408 1745177548033 GEN4_TO_CONTROLLER_LOG:GEN4_CONNECT_INT_LOG_AVR128DB48 VoltagesInfo: Values:
408 1745177548033 GEN4_TO_CONTROLLER_LOG:GEN4_CONNECT_INT_LOG_AVR128DB48 VoltagesInfo: internalVdd = 3300, internalVpp = 3300, targetVdd = 3300, targetVpp = 3300, vddSense = 3300, temp = 25000, vddCurrentSense = 0, vddVoltageSense = 3300
408 1745177548033 GEN4_TO_CONTROLLER_LOG:GEN4_CONNECT_INT_LOG_AVR128DB48 Return End

408 1745177548033 GEN4_TO_CONTROLLER_LOG:GEN4_CONNECT_INT_LOG_AVR128DB48 Pre:GetFirmwareInfo
408 1745177548033 GEN4_TO_CONTROLLER_LOG:GEN4_CONNECT_INT_LOG_AVR128DB48 Payload
408 1745177548033 GEN4_TO_CONTROLLER_LOG:GEN4_CONNECT_INT_LOG_AVR128DB48 null
408 1745177548033 GEN4_TO_CONTROLLER_LOG:GEN4_CONNECT_INT_LOG_AVR128DB48 Payload End
408 1745177548041 GEN4_TO_CONTROLLER_LOG:GEN4_CONNECT_INT_LOG_AVR128DB48 Post:GetFirmwareInfo
408 1745177548041 GEN4_TO_CONTROLLER_LOG:GEN4_CONNECT_INT_LOG_AVR128DB48 Return Value
408 1745177548041 GEN4_TO_CONTROLLER_LOG:GEN4_CONNECT_INT_LOG_AVR128DB48 FirmwareInfo: Values:
408 1745177548041 GEN4_TO_CONTROLLER_LOG:GEN4_CONNECT_INT_LOG_AVR128DB48 FirmwareInfo: boot = false, bootVer = 01.00.00, apVer = 02.01.06, fpgaVer = ff.ff.ff, scriptVer = 00.06.71, macAddress = 0495683578451535052485156485252, devID = a1020e01, devID1 = 1, devSN0 = ffffffff, devSN1 = ffffffff, serialNumber = 021038102RYN005698, appCommitID = null, scriptCommitID = 74cdf38a4d, PCB_ID = 2
408 1745177548041 GEN4_TO_CONTROLLER_LOG:GEN4_CONNECT_INT_LOG_AVR128DB48 Return End

408 1745177548041 GEN4_TO_CONTROLLER_LOG:GEN4_CONNECT_INT_LOG_AVR128DB48 Pre:SetToolInfo
408 1745177548041 GEN4_TO_CONTROLLER_LOG:GEN4_CONNECT_INT_LOG_AVR128DB48 Payload
408 1745177548041 GEN4_TO_CONTROLLER_LOG:GEN4_CONNECT_INT_LOG_AVR128DB48 ToolInfo: Values:
408 1745177548041 GEN4_TO_CONTROLLER_LOG:GEN4_CONNECT_INT_LOG_AVR128DB48 ToolInfo: speedLevel = 1, PGCResistance = 4700, PGDResistance = 4700, PGCPullDir = PullDown, PGDPullDir = PullDown, ICSPSelected = Wire2
408 1745177548041 GEN4_TO_CONTROLLER_LOG:GEN4_CONNECT_INT_LOG_AVR128DB48 Payload End
408 1745177548041 XXXX 1745177548041, Thread 408: XXXX 1745177548041, Entering Thread 408: Commands::runScriptBasic, script name = SetSpeed, timeOut = -1 ms  
408 1745177548042 XXXX 1745177548042, Thread 408: XXXX 1745177548042, Exiting Thread 408: Commands::runScriptBasic  
408 1745177548042 XXXX 1745177548042, Thread 408: XXXX 1745177548042, Entering Thread 408: Commands::runScriptBasic, script name = EnterProgMode, timeOut = -1 ms  
408 1745177548153 XXXX 1745177548153, Thread 408: XXXX 1745177548153, Exiting Thread 408: Commands::runScriptBasic  
408 1745177548153 GEN4_TO_CONTROLLER_LOG:GEN4_CONNECT_INT_LOG_AVR128DB48 Post:SetToolInfo
408 1745177548153 GEN4_TO_CONTROLLER_LOG:GEN4_CONNECT_INT_LOG_AVR128DB48 Return Value
408 1745177548153 GEN4_TO_CONTROLLER_LOG:GEN4_CONNECT_INT_LOG_AVR128DB48 none
408 1745177548153 GEN4_TO_CONTROLLER_LOG:GEN4_CONNECT_INT_LOG_AVR128DB48 Return End

408 1745177548153 GEN4_TO_CONTROLLER_LOG:GEN4_CONNECT_INT_LOG_AVR128DB48 Pre:GetTargetIDInfo
408 1745177548153 GEN4_TO_CONTROLLER_LOG:GEN4_CONNECT_INT_LOG_AVR128DB48 Payload
408 1745177548153 GEN4_TO_CONTROLLER_LOG:GEN4_CONNECT_INT_LOG_AVR128DB48 null
408 1745177548153 GEN4_TO_CONTROLLER_LOG:GEN4_CONNECT_INT_LOG_AVR128DB48 Payload End
408 1745177548156 XXXX 1745177548156, Thread 408: XXXX 1745177548156, Entering Thread 408: Commands::runScriptBasic, script name = EnterProgMode, timeOut = -1 ms  
408 1745177548267 XXXX 1745177548266, Thread 408: XXXX 1745177548266, Exiting Thread 408: Commands::runScriptBasic

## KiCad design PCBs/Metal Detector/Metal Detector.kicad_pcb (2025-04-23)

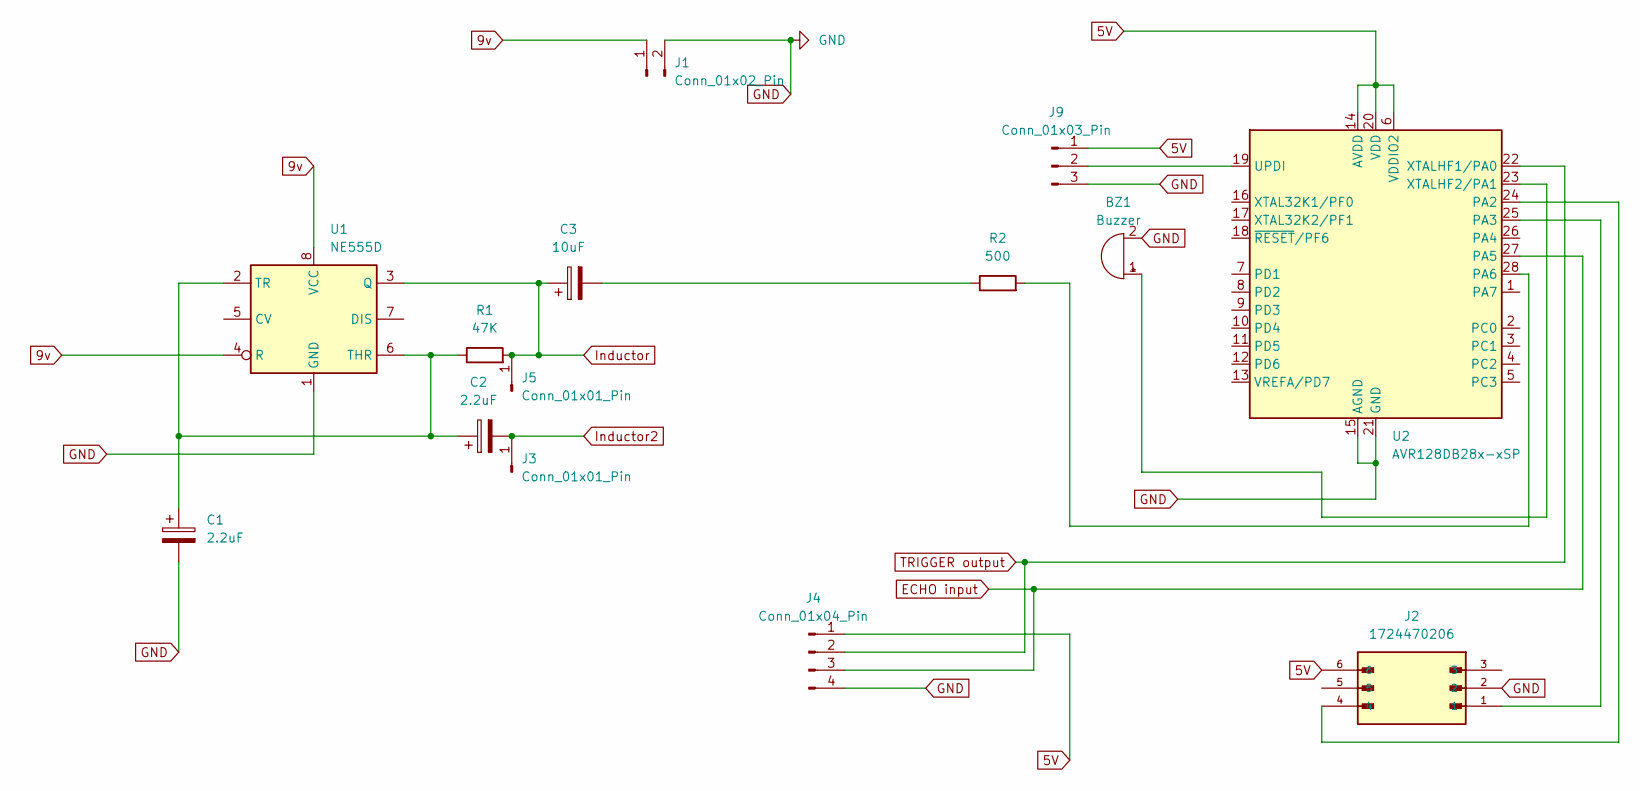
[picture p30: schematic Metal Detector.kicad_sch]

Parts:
BZ1: Buzzer; Buzzer_TDK_PS1240P02BT_D12.2mm_H6.5mm
C1, C2: 2.2uF; CP_Radial_D8.0mm_P2.50mm
C3: 10uF; CP_Radial_D8.0mm_P2.50mm
J1: Conn_01x02_Pin; PinHeader_2x01_P2.54mm_Vertical
J2: 1724470206; MOLEX_1724470206; PARTREV A6
J3, J5: Conn_01x01_Pin; PinSocket_1x01_P2.54mm_Vertical
J4: Conn_01x04_Pin; PinHeader_1x04_P2.54mm_Vertical
J9: Conn_01x03_Pin; PinHeader_1x03_P2.54mm_Vertical
R1: 47K; R_Axial_DIN0309_L9.0mm_D3.2mm_P12.70mm_Horizontal
R2: 500; R_Axial_DIN0309_L9.0mm_D3.2mm_P12.70mm_Horizontal
U1: NE555D; P8
U2: AVR128DB28x-xSP; SPDIP28_SP_MCH

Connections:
5V: J2.6, J4.1, J9.1, U2.6 (VDDIO2), U2.14 (AVDD), U2.20 (VDD)
9v: J1.1, U1.4 (R), U1.8 (VCC)
ECHO input: J4.3, U2.27 (PA5)
GND: BZ1.2 (-), C1.2, J1.2, J2.2, J4.4, J9.3, U1.1 (GND), U2.15 (AGND), U2.21 (GND)
Inductor: C3.1, J5.1, R1.2, U1.3 (Q)
Inductor2: C2.2, J3.1
unnamed: BZ1.1 (+), U2.23 (XTALHF2/PA1)
unnamed: C3.2, R2.1
unnamed: J9.2, U2.19 (UPDI)
unnamed: C1.1, C2.1, R1.1, U1.2 (TR), U1.6 (THR)
unnamed: J2.4, U2.24 (PA2)
unnamed: J2.1, U2.25 (PA3)
unnamed: R2.2, U2.28 (PA6)
TRIGGER output: J4.2, U2.22 (XTALHF1/PA0)

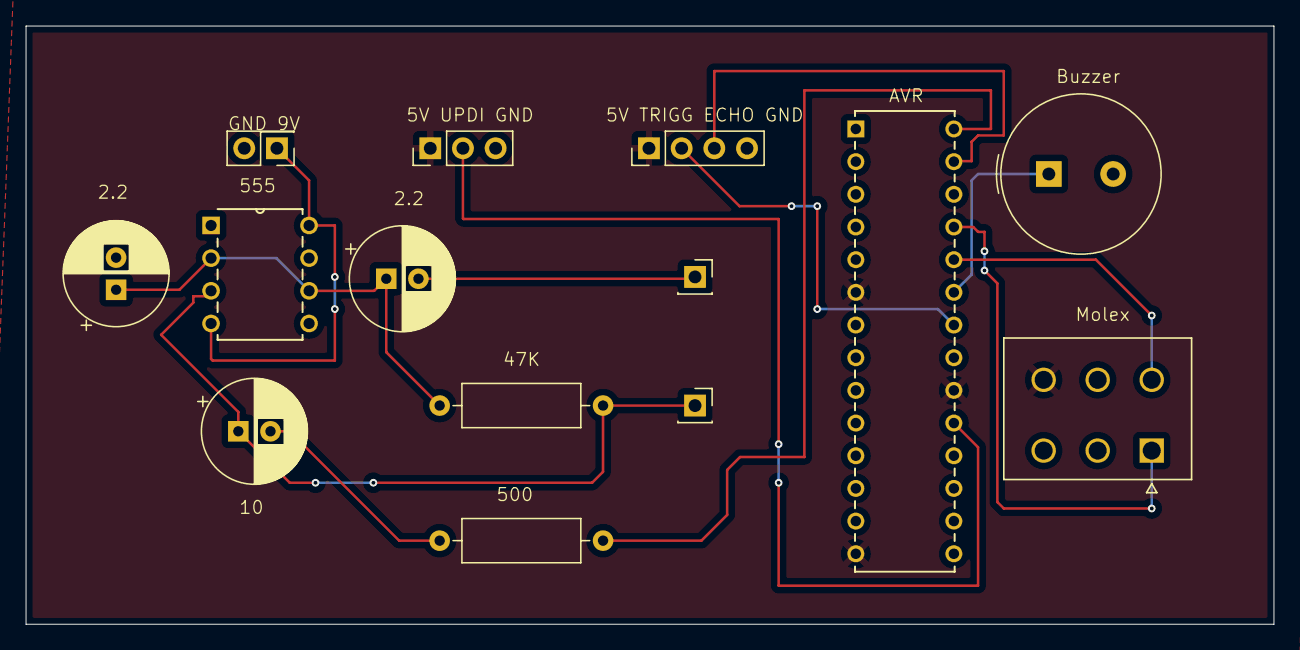
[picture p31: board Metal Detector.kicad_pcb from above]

Board: 2 copper layers, 97.0 x 46.5 mm, 14 parts (0 on the bottom side), 14 nets.

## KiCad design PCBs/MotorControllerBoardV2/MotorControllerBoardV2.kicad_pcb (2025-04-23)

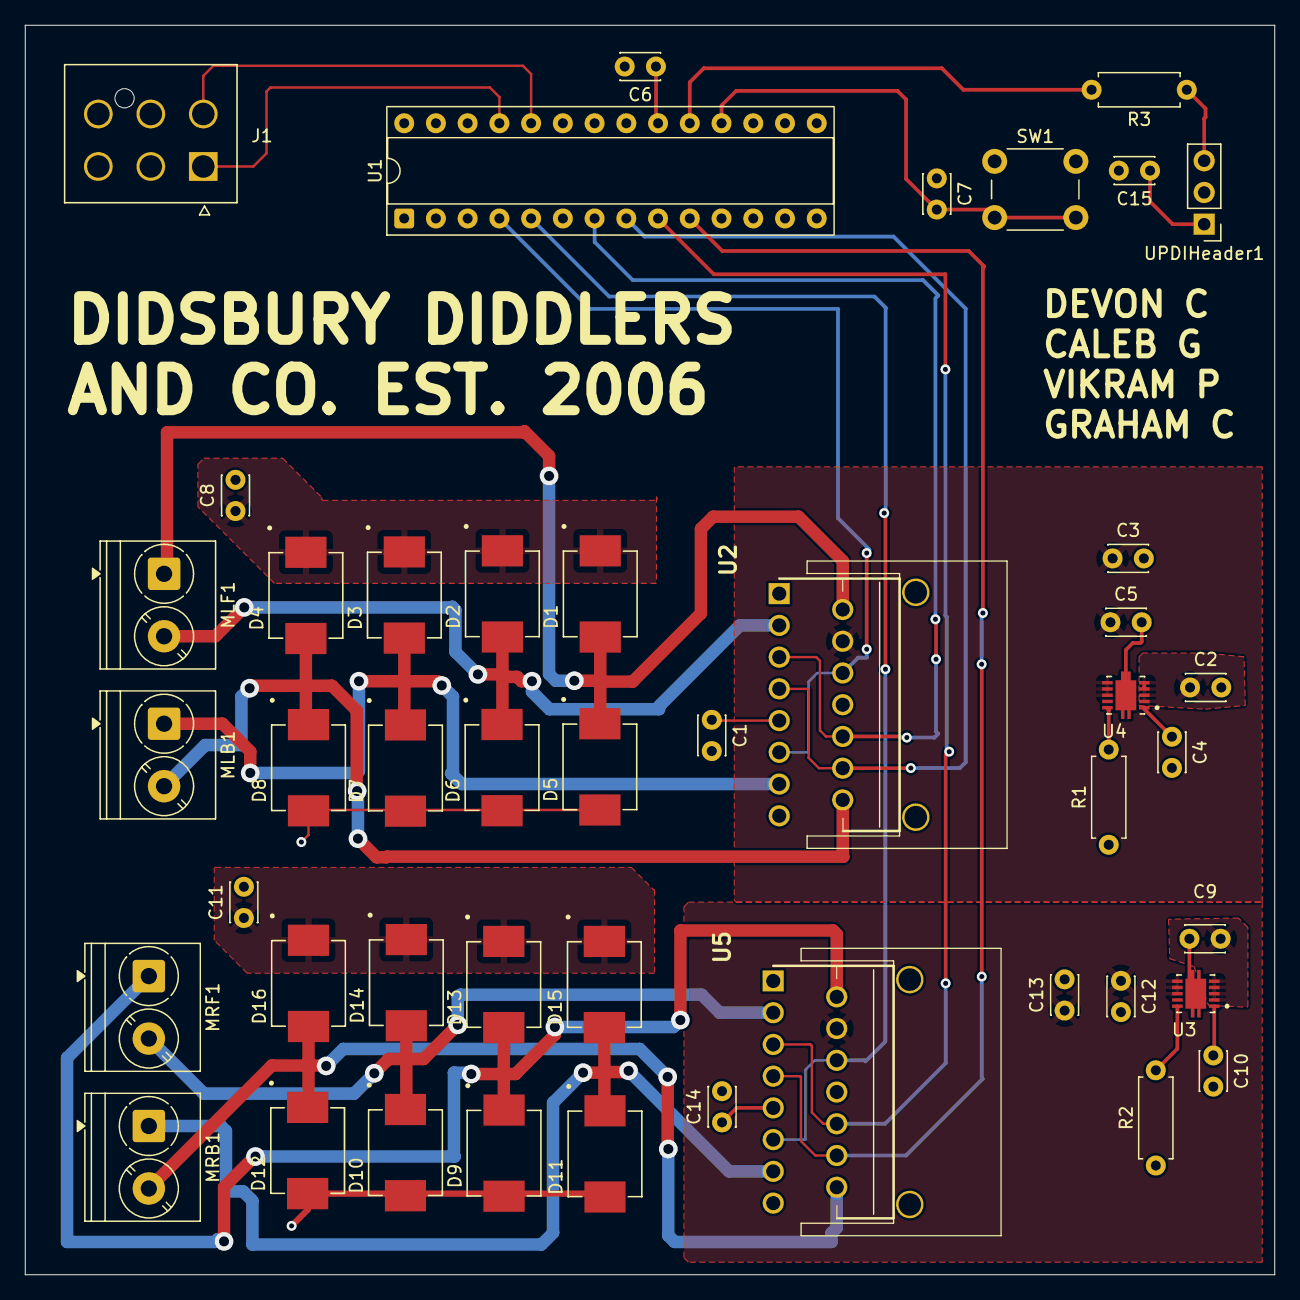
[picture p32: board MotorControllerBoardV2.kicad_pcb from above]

Board: 4 copper layers, 100.0 x 100.0 mm, 46 parts (0 on the bottom side), 28 nets.

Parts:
C1, C5, C13, C14: 100nF; C_Disc_D3.0mm_W2.0mm_P2.50mm
C2, C3, C6, C7, C9, C12, C15: 1μF; C_Disc_D3.0mm_W2.0mm_P2.50mm
C4, C10: 1nF; C_Disc_D3.0mm_W2.0mm_P2.50mm
C8, C11: 220μF; C_Disc_D3.0mm_W2.0mm_P2.50mm
D1, D2, D3, D4, D5, D6, D7, D8, D9, D10, D11, D12, D13, D14, D15, D16: B340-13-F; DIO_B340-13-F
J1: 2125201006; MOLEX_2125201006
MLB1: Screw_Terminal_2_P5.00mm; TerminalBlock_Phoenix_PT-1,5-2-5.0-H_1x02_P5.00mm_Horizontal
MLF1: Screw_Terminal_2_P5.00mm; TerminalBlock_Phoenix_PT-1,5-2-5.0-H_1x02_P5.00mm_Horizontal
MRB1: Screw_Terminal_2_P5.00mm; TerminalBlock_Phoenix_PT-1,5-2-5.0-H_1x02_P5.00mm_Horizontal
MRF1: Screw_Terminal_2_P5.00mm; TerminalBlock_Phoenix_PT-1,5-2-5.0-H_1x02_P5.00mm_Horizontal
R1, R2: 54.5k; R_Axial_DIN0207_L6.3mm_D2.5mm_P7.62mm_Horizontal
R3: 1.2k; R_Axial_DIN0207_L6.3mm_D2.5mm_P7.62mm_Horizontal
SW1: SW_Push; SW_PUSH_6mm
U1: AVR128DB28x-xSP; DIP-28_W7.62mm_Socket
U2, U5: L298N; Multiwatt15L V with heatsink v2
U3, U4: TCKE812NA_RF; IC_TCKE812NA_RF
UPDIHeader1: PINHD_1x3_Male; PinHeader_1x03_P2.54mm_Vertical

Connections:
5V Logic: C1.1 (+), C6.1 (+), C14.1 (+), C15.1 (+), J1.6, U1.6 (VDDIO2), U1.14 (AVDD), U1.20 (VDD), U2.9 (Vss), U5.9 (Vss), UPDIHeader1.1
7.2V Motor: C2.1 (+), C8.1 (+), C9.1 (+), C11.1 (+), D1.C, D2.C, D3.C, D4.C, D13.C, D14.C, D15.C, D16.C, J1.3, U3.2 (EN/UVLO), U3.3 (VIN), U3.4 (VIN), U3.5 (VIN), U4.2 (EN/UVLO), U4.3 (VIN), U4.4 (VIN), U4.5 (VIN)
GND: C1.2 (-), C2.2 (-), C3.2 (-), C4.2 (-), C5.2 (-), C6.2 (-), C7.1 (+), C8.2 (-), C9.2 (-), C10.2 (-), C11.2 (-), C12.2 (-), C13.2 (-), C14.2 (-), C15.2 (-), D5.A, D6.A, D7.A, D8.A, D9.A, D10.A, D11.A, D12.A, J1.2, R1.1 (+), R2.1 (+), SW1.1, U1.15 (AGND), U1.21 (GND), U2.1 (SENSE_A), U2.8 (GND), U2.15 (SENSE_B), U3.11 (GND), U4.11 (GND), U5.1 (SENSE_A), U5.8 (GND), U5.15 (SENSE_B), UPDIHeader1.2
LBWD: U1.8 (PD2), U2.7 (IN2), U2.12 (IN4)
LFWD: U1.7 (PD1), U2.5 (IN1), U2.10 (IN3)
LPWM: U1.4 (PC2), U2.6 (EnA), U2.11 (EnB)
unnamed: C3.1 (+), C5.1 (+), U2.4 (Vs), U4.6 (VOUT), U4.7 (VOUT), U4.8 (VOUT)
unnamed: C4.1 (+), U4.1 (DV/DT)
unnamed: C7.2 (-), SW1.2, U1.18 (~RESET/PF6)
unnamed: C10.1 (+), U3.1 (DV/DT)
unnamed: C12.1 (+), C13.1 (+), U3.6 (VOUT), U3.7 (VOUT), U3.8 (VOUT), U5.4 (Vs)
unnamed: R1.2 (-), U4.10 (ILIM)
unnamed: R2.2 (-), U3.10 (ILIM)
unnamed: R3.1 (+), UPDIHeader1.3
unnamed: R3.2 (-), U1.19 (UPDI)
unnamed: D1.A, D5.C, MLF1.1, U2.2 (OUT1)
unnamed: D2.A, D6.C, MLF1.2, U2.3 (OUT2)
unnamed: D3.A, D7.C, MLB1.1, U2.13 (OUT3)
unnamed: D4.A, D8.C, MLB1.2, U2.14 (OUT4)
unnamed: D9.C, D13.A, MRF1.1, U5.2 (OUT1)
unnamed: D10.C, D14.A, MRF1.2, U5.3 (OUT2)
unnamed: D11.C, D15.A, MRB1.1, U5.13 (OUT3)
unnamed: D12.C, D16.A, MRB1.2, U5.14 (OUT4)
RBWD: U1.10 (PD4), U5.7 (IN2), U5.12 (IN4)
RFWD: U1.9 (PD3), U5.5 (IN1), U5.10 (IN3)
RPWM: U1.5 (PC3), U5.6 (EnA), U5.11 (EnB)
SCL: J1.1, U1.25 (PA3)
SDA: J1.4, U1.24 (PA2)

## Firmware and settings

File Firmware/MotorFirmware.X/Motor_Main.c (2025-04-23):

#include <xc.h>

//******************************************************************************

// avr128db48-bare-metal-twi-mplab Main Initialization

//******************************************************************************

#include <avr/io.h>
#include <avr/interrupt.h>
#include <avr/eeprom.h>

#include "peripherals/CLKCTRL/CLKCTRL.h"
#include "peripherals/TWI/TWI_client.h"
#include "TWI_blockData.h"

FUSES = {
	.WDTCFG = 0x00, // WDTCFG {PERIOD=OFF, WINDOW=OFF}
	.BODCFG = 0x06, // BODCFG {SLEEP=SAMPLE, ACTIVE=ENABLE, SAMPFREQ=128Hz, LVL=BODLEVEL0}
	.OSCCFG = 0x00, // OSCCFG {CLKSEL=OSCHF}
	.SYSCFG0 = 0xC8, // SYSCFG0 {EESAVE=CLEAR, RSTPINCFG=RST, CRCSEL=CRC16, CRCSRC=NOCRC}
	.SYSCFG1 = 0x0C, // SYSCFG1 {SUT=8MS, MVSYSCFG=DUAL}
	.CODESIZE = 0x00, // CODESIZE {CODESIZE=User range:  0x0 - 0xFF}
	.BOOTSIZE = 0x00, // BOOTSIZE {BOOTSIZE=User range:  0x0 - 0xFF}
};

LOCKBITS = 0x5CC5C55C; // {KEY=NOLOCK}

#define DATA_SIZE 16

#define RIGHT 1
#define LEFT 0

//******************************************************************************

// Didsbury Diddlers Proprietary Function Definitions

//******************************************************************************

// Fairly sure that his clock setup is handled in the library

//// === CLOCK SETUP ===
//void setup_clock() {
//    CCP = 0xD8;
//    CLKCTRL.OSCHFCTRLA = 0b00010100;      // Set 16 MHz internal oscillator
//    while (CLKCTRL.MCLKSTATUS & 0b00000001); // Wait for clock switch to complete
//}


// === PIN SETUP ===
void setup_pins() {
    PORTMUX.TCAROUTEA = 0b00000010;
    PORTC.DIRSET = 0b00001100;            // PC2 (TCB0), PC3 (TCB1) as PWM outputs
    PORTD.DIRSET = 0b00011110;            // PD1–PD4 as motor direction control outputs
}

// === PWM SETUP ===
void setup_pwm() {
    TCA0.SPLIT.CTRLESET = 0b00001100;
    TCA0.SPLIT.CTRLD = 0b00000001;
    TCA0.SPLIT.LPER = 0xff;
    TCA0.SPLIT.HPER = 0xff;
    
    TCA0.SPLIT.HCMP0 = 0x00; // for right pwm, PC3
    TCA0.SPLIT.LCMP2 = 0x00; // for left pwm, PC2
    
    TCA0.SPLIT.CTRLB = 0b00010100;
    
    TCA0.SPLIT.CTRLA = 0b00000001;
    
}

// === MOTOR CONTROL FUNCTION ===
void drive_motor(uint8_t sm, uint8_t side) {
    uint8_t sign = sm & 0x80;             // Bit 7 = direction
    uint8_t magnitude = sm & 0x7F;        // Bits 6–0 = speed

    if(side == RIGHT){
        if (sign) {
            PORTD.OUTSET = (1 << 4);    // Set backward pin high
            PORTD.OUTCLR = (1 << 3);    // Clear forward pin
        } 
        else {
            PORTD.OUTSET = (1 << 3);    // Set forward pin high
            PORTD.OUTCLR = (1 << 4);    // Clear backward pin
        }
        // set PWM duty 0-ff for right side
        TCA0.SPLIT.HCMP0 = magnitude << 1;
    }
    else if (side == LEFT){
        if (sign) {
            PORTD.OUTSET = (1 << 2);    // Set backward pin high
            PORTD.OUTCLR = (1 << 1);    // Clear forward pin
        } else {
            PORTD.OUTSET = (1 << 1);    // Set forward pin high
            PORTD.OUTCLR = (1 << 2);    // Clear backward pin
        }
        // set PWM duty 0-ff for right side
        TCA0.SPLIT.LCMP2 = magnitude << 1;
    }
}

//******************************************************************************

// Main

//******************************************************************************

// === MAIN LOOP ===
int main(void) {
    
    setup_pins();                         // Set up direction and PWM pins
    setup_pwm();                          // Configure PWM for TCB0 and TCB1
       
    //Setup CPU Clocks
    CLKCTRL_init();
    
    //Setup TWI I/O
    TWI_initPins();
    
    //Setup TWI Interface
    TWI_initClient(0x11); // Initialize client address as 0x11
    
    //Data to R/W to. (Must be volatile)
    volatile uint8_t data[DATA_SIZE];
    
    //Initialize Memory to 0x00
    for (uint8_t i = 0; i < DATA_SIZE; i++)
    {
        data[i] = 0x00;
    }
    
    //Attach R/W Buffers
    //Note: The buffers can be separated, or they can be the same memory, if desired.
    setupReadBuffer(&data[0], 16);
    setupWriteBuffer(&data[8], 8);
    
    //Assign ISRs to Block Memory Library
    TWI_assignByteWriteHandler(&_TWI_StoreByte);
    TWI_assignByteReadHandler(&_TWI_RequestByte);
    TWI_assignStopHandler(&_onTWIStop);
    
    //Enable Interrupts
    sei();

//******************************************************************************
    
  // Super Loop  

//******************************************************************************
    
    // Responsible for motor control from ECU I2C data. Sending left then right
    // motor data.
    
    while (1)
    {   
        
        drive_motor(data[8], LEFT);   // PD1 = FWD, PD2 = BWD (left)
        drive_motor(data[9], RIGHT);  // PD3 = FWD, PD4 = BWD (right)
    }
}

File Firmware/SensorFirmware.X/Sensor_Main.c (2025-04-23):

#include <xc.h>

//******************************************************************************

// avr128db48-bare-metal-twi-mplab Main Initialization

//******************************************************************************

#include <avr/io.h>
#include <avr/interrupt.h>
#include <avr/eeprom.h>

#include "peripherals/CLKCTRL/CLKCTRL.h"
#include "peripherals/TWI/TWI_client.h"
#include "TWI_blockData.h"

#define DATA_SIZE 16

#define VALUE_U_SIZE 8

/* --------- GLOBAL VARS DECLARATION ------------- */
uint16_t value_u[VALUE_U_SIZE];
uint8_t value[5];
uint8_t count_u = 0;
uint8_t tally_u = 0;
uint8_t count = 0;
uint8_t tally = 0;
//uint8_t duty = 25000;
float distance = 0.0;
float distance_final = 0.0;

//Data to R/W to. (Must be volatile)
volatile uint8_t data[DATA_SIZE];

void SensorInitialization(){
    PORTA.DIRSET = 0b00000011;   //PA0 and PA1 set as output
    TCA0.SINGLE.CTRLA = (0x01)<<3 | 0x01;//divide by 16 and enable clk
    TCA0.SINGLE.CTRLB = 0x03;   //single slope PWM
    TCA0.SINGLE.CTRLB |= 0x01 << 4; //PA0 enabled
    TCA0.SINGLE.PER = 31249; //value calculated to produce trigger pulse
    TCA0.SINGLE.CMP0 = 6; //set to very low duty for trigger pulse
    EVSYS.CHANNEL0 = 0x45;    //PORTA pin PA5 as echo input
    EVSYS.USERTCB2CAPT = 0x01;  //Choose channel 0
    TCB2.INTCTRL = 0x01; //Capture interupt enable
    TCB2.EVCTRL = 0x01; //enable input capture event
    TCB2.CTRLB = 0x04; //PWM measurement mode
    TCB2.CTRLA = 0x01; //TCB enable
    EVSYS.CHANNEL1 = 0x46;    //PORTA pin PA6 for metal detector
    EVSYS.USERTCB1CAPT = 0x02;  //Choose channel 1
    TCB1.INTCTRL = 0x01; //Capture interupt enable
    TCB1.EVCTRL = 0x01; //enable input capture event
    TCB1.CTRLB = 0x03; //Frequency measurement mode
    TCB1.CTRLA = 0x01; //TCB enable
}

/* ------ Define ISR -----*/
ISR(TCB2_INT_vect){
    TCB2.INTFLAGS = 0x01; //clears flag
    TCA0.SINGLE.CMP0 = 6;
    value_u[count_u] = TCB2.CCMP;
    count_u++;
    count_u %= VALUE_U_SIZE; // used later to average TCB.CCMP for distance measuring
    long averageDist = 0;
    //RMS might be appropriate for emphasizing the larger values.
    for (int i = 0; i < VALUE_U_SIZE; i++){
       averageDist += value_u[i]; //averages TCB.CCMP for distance measuring
    }
    averageDist = averageDist >> 3;
    data[0] = (averageDist & 0xFE) | (data[0] & 0b00000001);
    data[1] = averageDist >> 8;
}

ISR(TCB1_INT_vect){
    TCB1.INTFLAGS = 0x01; //clears flag
    value[count] = TCB1.CCMP;
    if(value[count] < 200){ 
        tally++;
    }
    count++;
    if(count >= 5){ //if five consecutive values read metal, detect the metal.
        if(tally == 5){
            PORTA.OUT = 0b00000010; 
            data[0] |= 0x01;
        }else{
            PORTA.OUT = 0b00000000;
            data[0] &= 0xFE;
        }
        count = 0;
        tally = 0;
    }
}

// === MAIN FUNCTION ===
int main(void) {
    //Setup CPU Clocks
    CLKCTRL_init();
    
    // Sensor Initialization
    SensorInitialization();
    
    //Setup TWI I/O
    TWI_initPins();
    
    //Setup TWI Interface
    TWI_initClient(0x22); // Initialize client address as 0x22
    
    
    //Initialize Memory to 0x00
    for (uint8_t i = 0; i < DATA_SIZE; i++)
    {
        data[i] = 0x00;
    }
    
    //Attach R/W Buffers
    //Note: The buffers can be separated, or they can be the same memory, if desired.
    setupReadBuffer(&data[0], 16);
    setupWriteBuffer(&data[8], 8);
    
    //Assign ISRs to Block Memory Library
    TWI_assignByteWriteHandler(&_TWI_StoreByte);
    TWI_assignByteReadHandler(&_TWI_RequestByte);
    TWI_assignStopHandler(&_onTWIStop);
    
    //Enable Interrupts
    sei();
    
    while (1)
    {   
    }
}

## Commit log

2025-04-02 Started doing radioSPI driver
2025-04-04 SPI Radio Stuff
2025-04-05 Updated radio SPI
2025-04-07 Updated SPI radio to hopefully function
2025-04-08 Fixing SS
    Fixed SS by moving transfer stalls
2025-04-08 Created I2C Library Prototype
2025-04-09 I2C Libraries
2025-04-09 I2C config
2025-04-19 Potential Motor Data Transfer
2025-04-20 Added Sensor board
2025-04-20 Added Sensor Board Code
2025-04-20 Sensor board works!
2025-04-21 Motor, Sensor, and Controller Integration
2025-04-21 Fixed some controller firmware
    [Controller_Main.c, LCD.c]
2025-04-22 Added some Comments
    Fixed the boot sequence, optimized some code, and added comments.
    [Controller_Main.c, ECU-main.c, LCD.c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]
2025-04-22 Switch works
2025-04-23 Changed folder name
    [ENEL300_Motor_Bracket_T v4.stl, ENEL300_Tire_D_Type v1.stl, ENEL300_Tire_Outer_v1 v2.stl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]
2025-04-23 Metal Detector
    [Metal Detector-B_Cu.gbr, Metal Detector-B_Mask.gbr, Metal Detector-B_Paste.gbr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]
2025-04-23 Added Devons PCB
    [2125201006.PcbLib, 2125201006.SchLib, L298N.PcbLib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]
